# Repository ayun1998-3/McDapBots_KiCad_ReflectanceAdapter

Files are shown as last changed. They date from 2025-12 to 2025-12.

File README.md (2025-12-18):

# McDap Bots Pedagogical Robot

This project was created as a capstone project for the University of Virginia Department of Electrical and Computer Engineering. Our goal was to create a small robot which could be programmed by students, for use as a teaching aide in an embedded systems course. This repository contains the software component of this, both drivers and application code.

**Authors**
- Colby Wise
- Pratik Pandit
- Austen Yun 
- David Merino
- Marc Rosenthal

**Advisors**: Todd DeLong and Adam Barnes 

**Features at a glance**
- 2 motors (PWM controlled), OLED screen (I2C), reflectance sensor (I2C), bump switches (GPIO), Bluetooth (UART), and infrared sensors (ADC)
- battery charging port and battery voltage display (press button to enable)
- support for TI and STM microcontrollers

## What is contained here
This repository contains a KiCad project file for the reflectance sensor adapter board, which connects the [15-Channel Reflectance Sensor Array](https://www.pololu.com/product/4315) to
the robot's main PCB. The reflectance sensor board can be soldered onto this adapter board via male header pins, and this adapter board has pins that plug into the bottom of the main PCB.

**Schematic File**

KiCad schematic file that shows the electrical connections of the reflectance sensor adapter board. 

**Layout File**

KiCad layout file that shows how the components are placed and routed on the reflectance sensor adapter board.

**Bill of Materials Files**

BOM.xlsx contains a list of all the parts needed for to add the reflectance sensor as a feature to the robot.
Digikey_Parts_List.xlsx can be uploaded to Digikey to select the parts needed for one copy of this board.

## How to use this repository
1. Copy the repository locally to your computer
2. Using KiCad 8.0 (or higher version) open the file `Reflectance_Adapter.kicad_pro"`
3. Generate necessary gerber files and order components

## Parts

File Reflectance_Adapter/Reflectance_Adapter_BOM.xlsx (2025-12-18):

Reflectance Sensor Adapter Board Parts
Id | Designator | Footprint | Quantity | Designation | Supplier | Link | Notes
1 | J1, J4 | PinHeader_1x04_P2.54mm_Vertical | 2 | Reflector I2C, Support | Digikey | 0879370800 Molex | Connectors, Interconnects | DigiKey (https://www.digikey.com/en/products/detail/molex/0879370800/3303582) | Long 4-pin male header
2 | U1 | TSSOP-24_4.4x7.8mm_P0.65mm | 1 | TCA9555PWR | Digikey | TCA9555PWR Texas Instruments | Integrated Circuits (ICs) | DigiKey (https://www.digikey.com/en/products/detail/texas-instruments/TCA9555PWR/2094642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) | GPIO to I2C expander
3 | J2 | PinSocket_1x08_P2.54mm_Vertical | 1 | Conn_QTRX_Top_Row | Digikey | TSW-120-07-L-S Samtec Inc. | Connectors, Interconnects | DigiKey (https://www.digikey.com/en/products/detail/samtec-inc/tsw-120-07-l-s/1101407) | 8-pin male header, soldered onto both reflectance sensor board and adapter board
4 | J3 | PinSocket_1x11_P2.54mm_Vertical | 1 | Conn_QTRX_Bot_Row | Digikey | TSW-120-07-L-S Samtec Inc. | Connectors, Interconnects | DigiKey (https://www.digikey.com/en/products/detail/samtec-inc/tsw-120-07-l-s/1101407) | 11-pin male header, soldered onto both reflectance sensor board and adapter board
Additional Parts
Id | Designator | Footprint | Quantity | Designation | Supplier | Link | Notes
1 |  |  | 1 | QTRX-HD-15RC Reflectance Sensor Array | Pololu | Pololu - QTRX-HD-15RC Reflectance Sensor Array: 15-Channel, 4mm Pitch, RC Output, Low Current (https://www.pololu.com/product/4315) | 15-Channel Reflectance Sensor Array Board from Pololu

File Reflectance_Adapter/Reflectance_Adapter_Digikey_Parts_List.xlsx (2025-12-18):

Digikey Parts List
Manufacturer Part Number | Digikey Part Number | Quantity | Designator | Link | Notes
879370800 | WM23650-ND | 2 | J1, J4 | 0879370800 Molex | Connectors, Interconnects | DigiKey (https://www.digikey.com/en/products/detail/molex/0879370800/3303582) | Long 4-pin male headers for J1 and J4
TCA9555PWR | 296-24827-2-ND | 1 | U1 | TCA9555PWR Texas Instruments | Integrated Circuits (ICs) | DigiKey (https://www.digikey.com/en/products/detail/texas-instruments/TCA9555PWR/2094642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) | GPIO to I2C expander
TSW-120-07-L-S | SAM1031-20-ND | 1 | J2, J3 | TSW-120-07-L-S Samtec Inc. | Connectors, Interconnects | DigiKey (https://www.digikey.com/en/products/detail/samtec-inc/tsw-120-07-l-s/1101407) | 20-pin male header for the 8-pin and 11-pin male headers

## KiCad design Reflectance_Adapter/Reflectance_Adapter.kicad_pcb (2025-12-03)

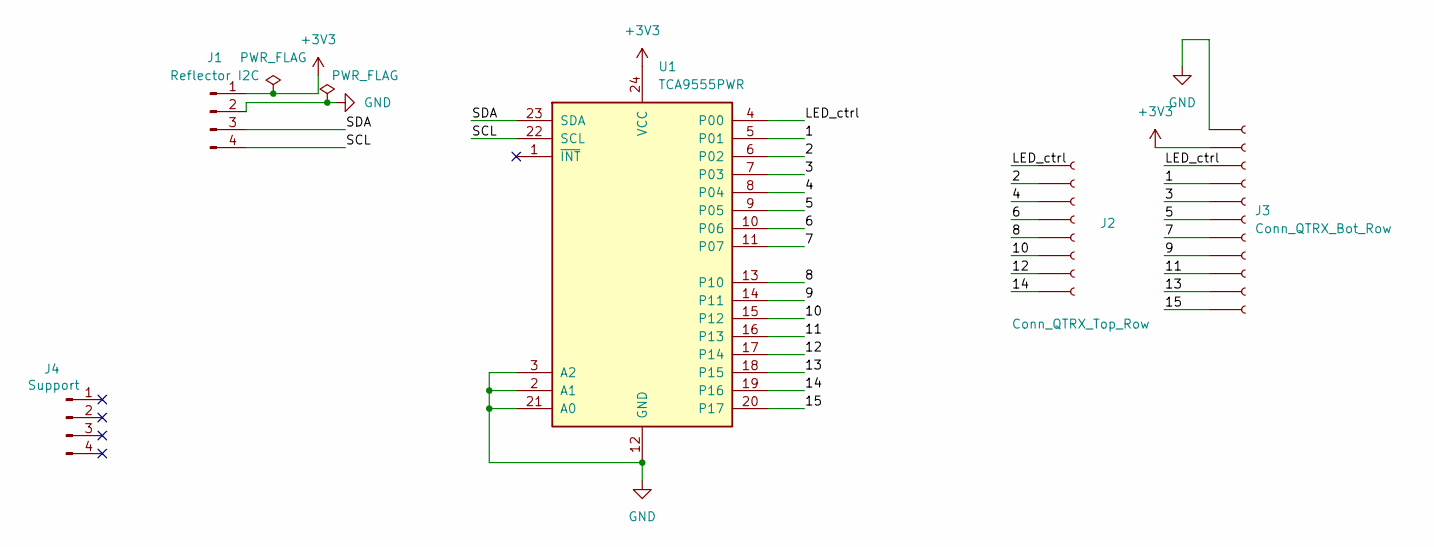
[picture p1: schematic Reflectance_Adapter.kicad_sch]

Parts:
J1: Reflector I2C; PinHeader_1x04_P2.54mm_Vertical
J2: Conn_QTRX_Top_Row; PinSocket_1x08_P2.54mm_Vertical
J3: Conn_QTRX_Bot_Row; PinSocket_1x11_P2.54mm_Vertical
J4: Support; PinHeader_1x04_P2.54mm_Vertical
U1: TCA9555PWR; TSSOP-24_4.4x7.8mm_P0.65mm

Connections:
+3V3: J1.1, J3.2, U1.24 (VCC)
/1: J3.4, U1.5 (P01)
/2: J2.2, U1.6 (P02)
/3: J3.5, U1.7 (P03)
/4: J2.3, U1.8 (P04)
/5: J3.6, U1.9 (P05)
/6: J2.4, U1.10 (P06)
/7: J3.7, U1.11 (P07)
/8: J2.5, U1.13 (P10)
/9: J3.8, U1.14 (P11)
/10: J2.6, U1.15 (P12)
/11: J3.9, U1.16 (P13)
/12: J2.7, U1.17 (P14)
/13: J3.10, U1.18 (P15)
/14: J2.8, U1.19 (P16)
/15: J3.11, U1.20 (P17)
/LED_ctrl: J2.1, J3.3, U1.4 (P00)
/SCL: J1.4, U1.22 (SCL)
/SDA: J1.3, U1.23 (SDA)
GND: J1.2, J3.1, U1.2 (A1), U1.3 (A2), U1.12 (GND), U1.21 (A0)

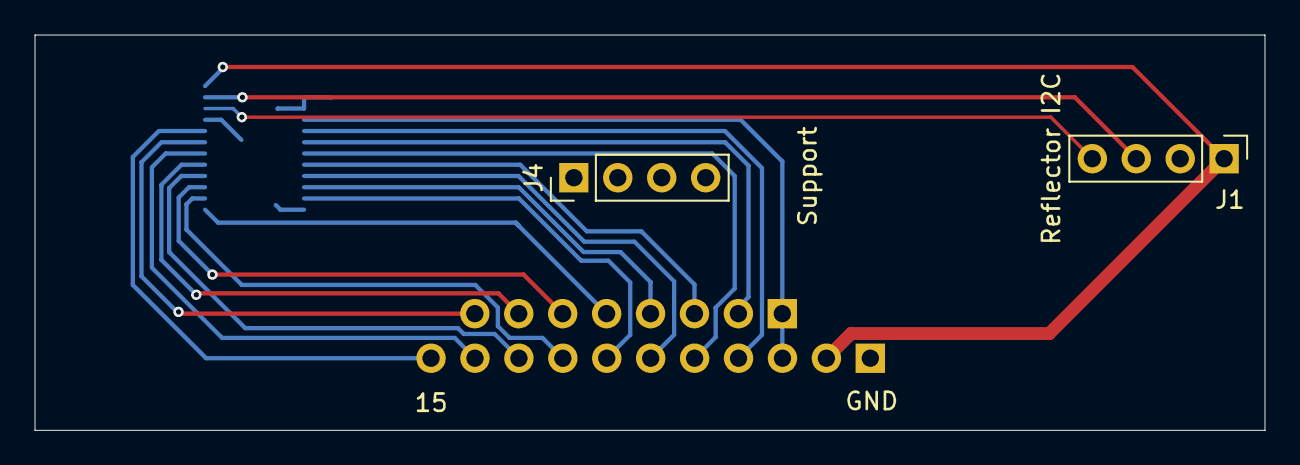
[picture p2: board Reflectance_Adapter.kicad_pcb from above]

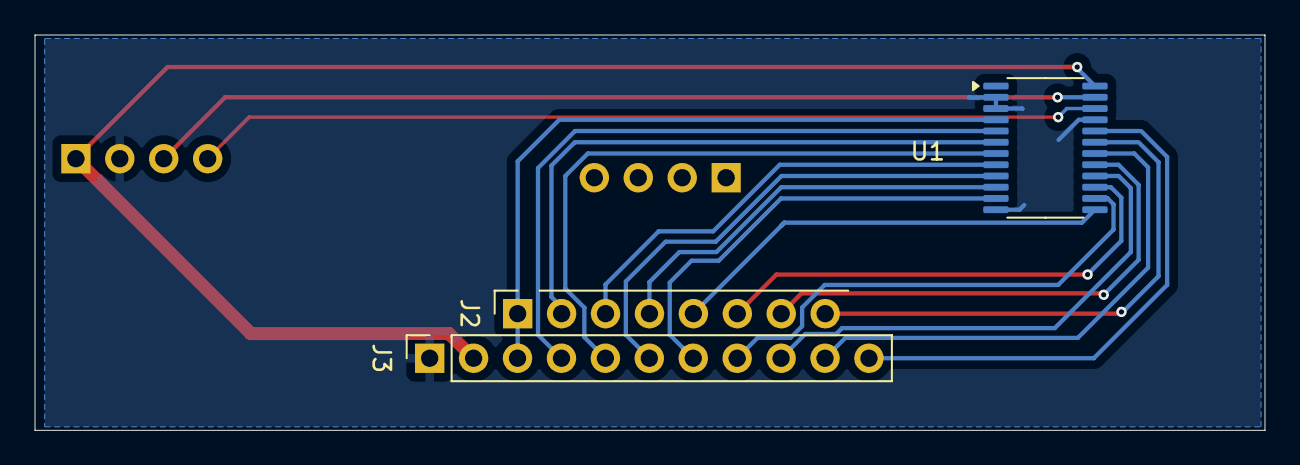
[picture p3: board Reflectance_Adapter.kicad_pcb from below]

Board: 2 copper layers, 71.1 x 22.9 mm, 5 parts (3 on the bottom side), 20 nets.

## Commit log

2025-10-09 Created empty KiCad project
    [Reflectance_Adapter.kicad_pcb, Reflectance_Adapter.kicad_sch]
2025-10-09 Completed schematic
    [Reflectance_Adapter.kicad_sch]
2025-10-09 Assigned footprints
    [Reflectance_Adapter.kicad_pcb, Reflectance_Adapter.kicad_sch]
2025-10-10 Completed layout
    User layer 1 contains dimensions of Pololu reflectance sensor array board. User layer 8 contains dimensions of slots of Pololu Chassis (copied over from the MSPM0 kicad project)
    [Reflectance_Adapter.kicad_pcb, Reflectance_Adapter.kicad_sch]
2025-10-15 Added text to silkscreen
    Also generated Gerbers
    [Reflectance_Adapter-B_Cu.gbl, Reflectance_Adapter-B_Mask.gbs, Reflectance_Adapter-B_Paste.gbp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]
2025-12-03 corrected i2c pin positions
    [Reflectance_Adapter-B_Cu.gbl, Reflectance_Adapter-B_Mask.gbs, Reflectance_Adapter-B_Paste.gbp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]
2025-12-18 Added BOM and digikey parts list files
    [BOM.xlsx, Digikey_Parts_List.xlsx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]
2025-12-18 Update README.md
    Update README.md with info about BOM and digikey parts list
2025-12-18 Closed kicad project
2025-12-18 Reformatted some files
    [BOM.xlsx, Digikey_Parts_List.xlsx, Reflectance_Adapter_BOM.xlsx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]
